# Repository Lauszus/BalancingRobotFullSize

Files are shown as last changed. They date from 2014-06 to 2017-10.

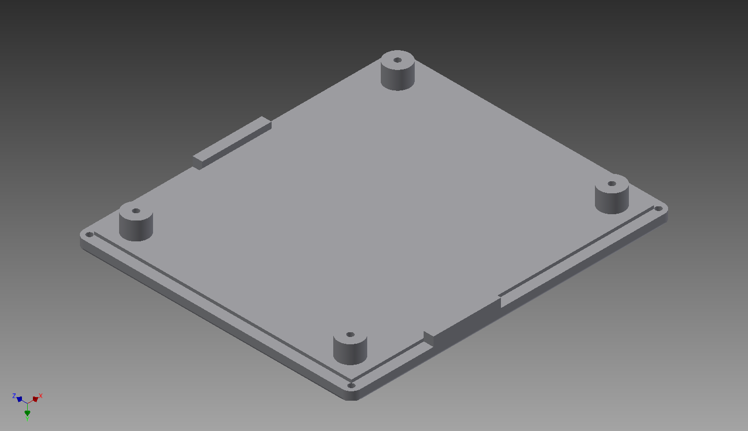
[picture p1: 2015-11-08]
MotorDriverEnclosure/MotorDriverEnclosure_lid.png

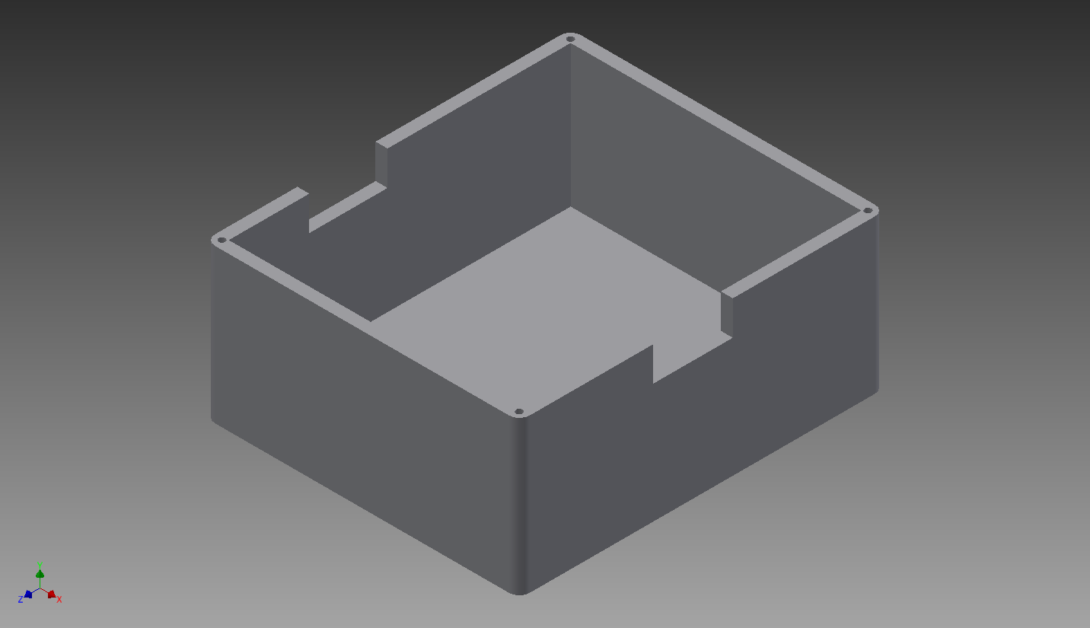
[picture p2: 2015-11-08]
MotorDriverEnclosure/MotorDriverEnclosure.png

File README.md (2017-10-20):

# Balancing robot full size
#### Developed by Kristian Sloth Lauszus and Mads Friis Bornebusch, 2014

The code is released under the GNU General Public License.
_________

This is the code for my full size balancing robot.

Both our paper and poster can be found inside the [Documents](Documents) directory.

Detailed information can be found at the blog post: <http://blog.tkjelectronics.dk/2014/07/full-size-diy-balancing-robot/>.



## Android application



I have also written an Android application for the robot. The source code is available at the following link: <https://github.com/Lauszus/BalancingRobotFullSizeAndroid>.



For more information send me an email at <lauszus@gmail.com>.

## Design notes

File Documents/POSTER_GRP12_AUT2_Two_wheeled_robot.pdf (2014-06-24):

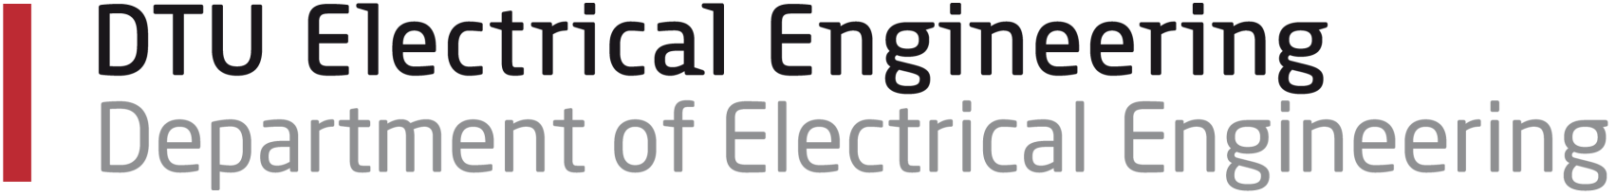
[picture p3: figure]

# Two Wheeled Balancing Robot

# Mads Bornebusch (s123627) Kristian Lauszus (s123808)

Abstract The goal of the project is to build a two wheeled self-balancing robot capable of carrying a person. The dynamics of the robot is found and the system is simulated and stabilized with a controller in Matlab. The robot is programmed in C/C++ on an 8-bit ATmega328P AVR microcontroller. A manually tuned PID-controller is used to keep it balanced. The robot is able to communicate with an

Android device over a two way Bluetooth connection.

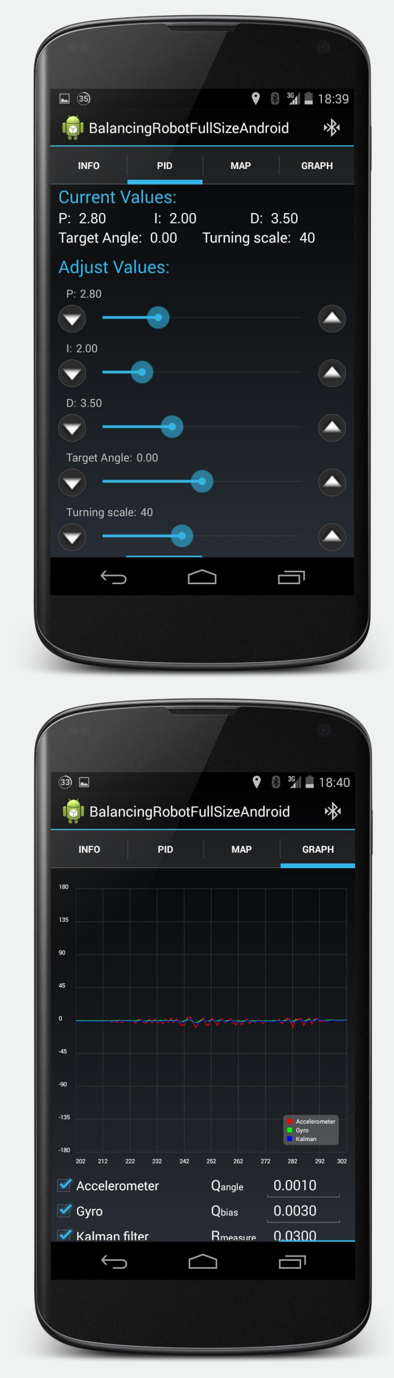
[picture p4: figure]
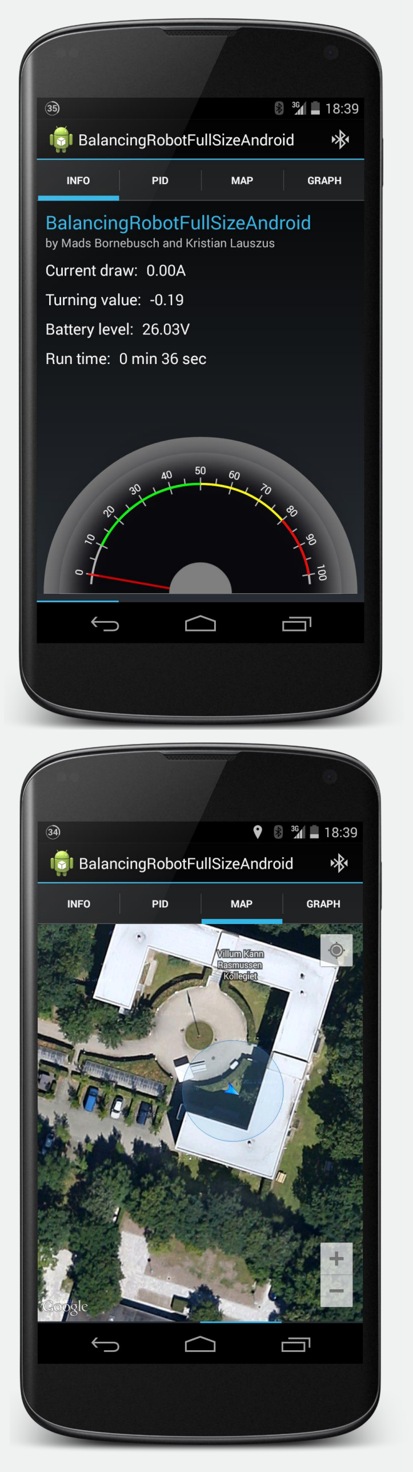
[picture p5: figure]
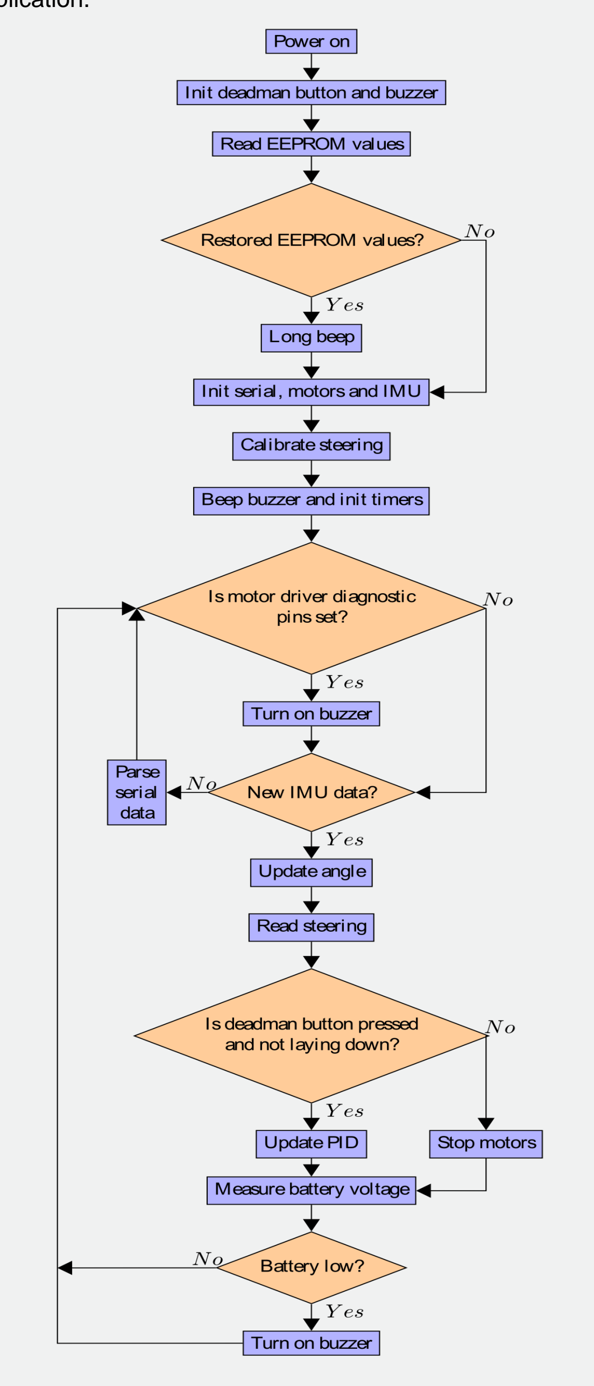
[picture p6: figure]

## Fig. 4 – Andriod Application The figure shows

screenshots of the four different screens in the Android application written for the robot. Top left: This screen shows different values that is sent from the robot to the app. This is general information for the user such as current draw, battery level and PWM-value. Top right: This screen is for adjusting the PID-values for the controller. This is used for tuning the robot to make it balance. The user can also set the target angle and how aggressively the robot is turning. Bottom left: This screen is showing the user a map with the current position of the robot using the Android device’s built in GPS. This can be used for navigation and to see which attractions are nearby. Bottom right: This screen is showing a graph with the angle taken from the gyroscope, the accelerometer and from the Kalman filter.
Protocol: In order to make sure that the data is parsed properly between the robot and the Android application, a protocol for this was implemented. It consists of a constant string header, one byte to indicate the command and one byte indicating the length of the data to follow. After the data there is a checksum calculated by taking XOR of all bytes in the message excluding the header.

## Fig. 3 – Code for the Robot The figure below

shows a flowchart of the code running on the robot. The code for the robot is written in C/C++, using some libraries and functions from the open source platform Arduino. The code consists of a part that initializes the system followed by an infinite loop that balances the robot and sends data to the Android application via Bluetooth. Initialization: When the robot is started up, values are read from the EEPROM, outputs and inputs are initialized on the microcontroller and the steering is calibrated. Main loop: The main loop is checking for IMU-data, updating PID-values, measuring battery voltage and sending serial data via the Bluetooth module to the Android application.

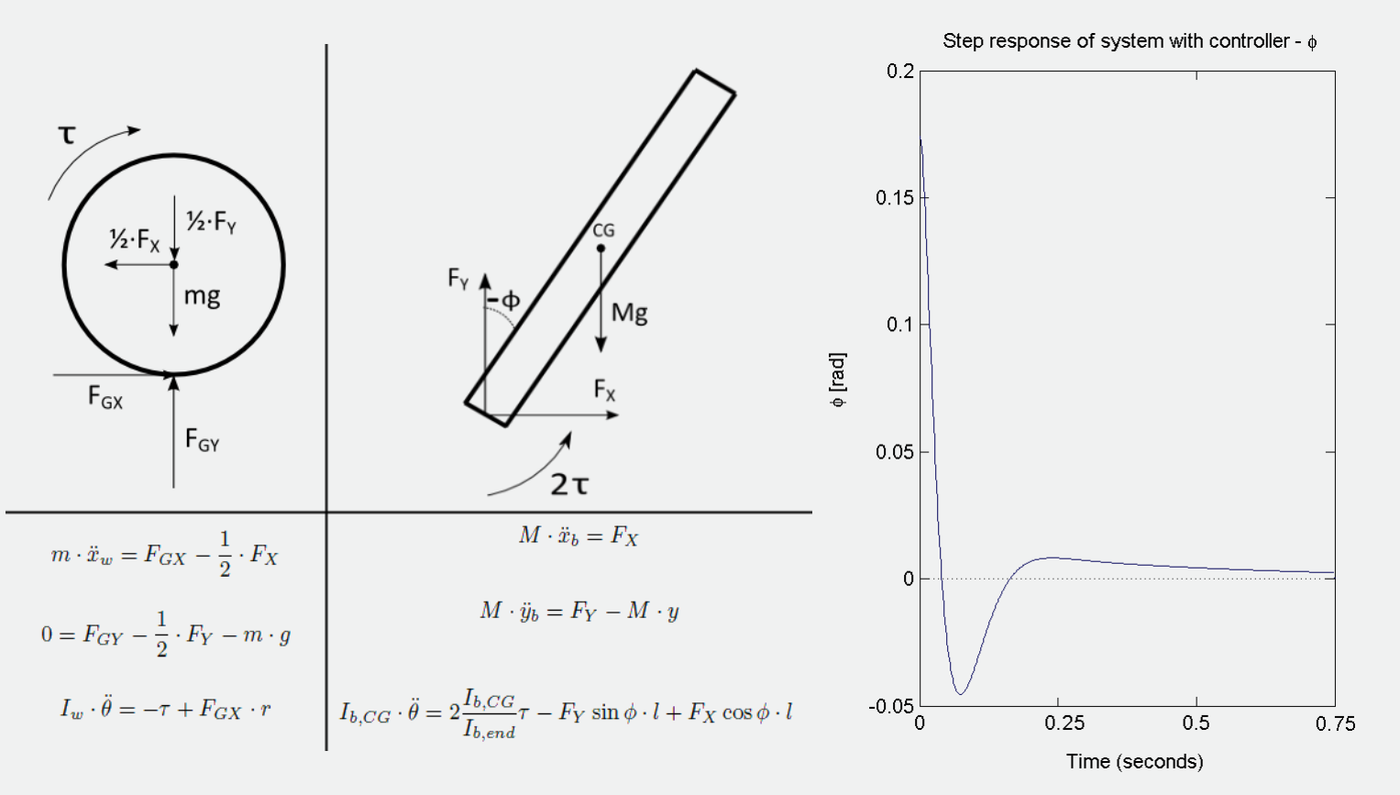
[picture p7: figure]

## Fig. 1 – Model and simulations Using the free

body diagrams to the left, the equations for the robot is set up (left bottom). These lead to a transfer function from τ to φ for the robot and a controller can be designed in Matlab. The controller is designed by choosing ωc which is the cross frequency of the Bode plot of the system. The step response with the controller inserted is shown to the right. It can be seen that it is indeed possible to stabilise the system.

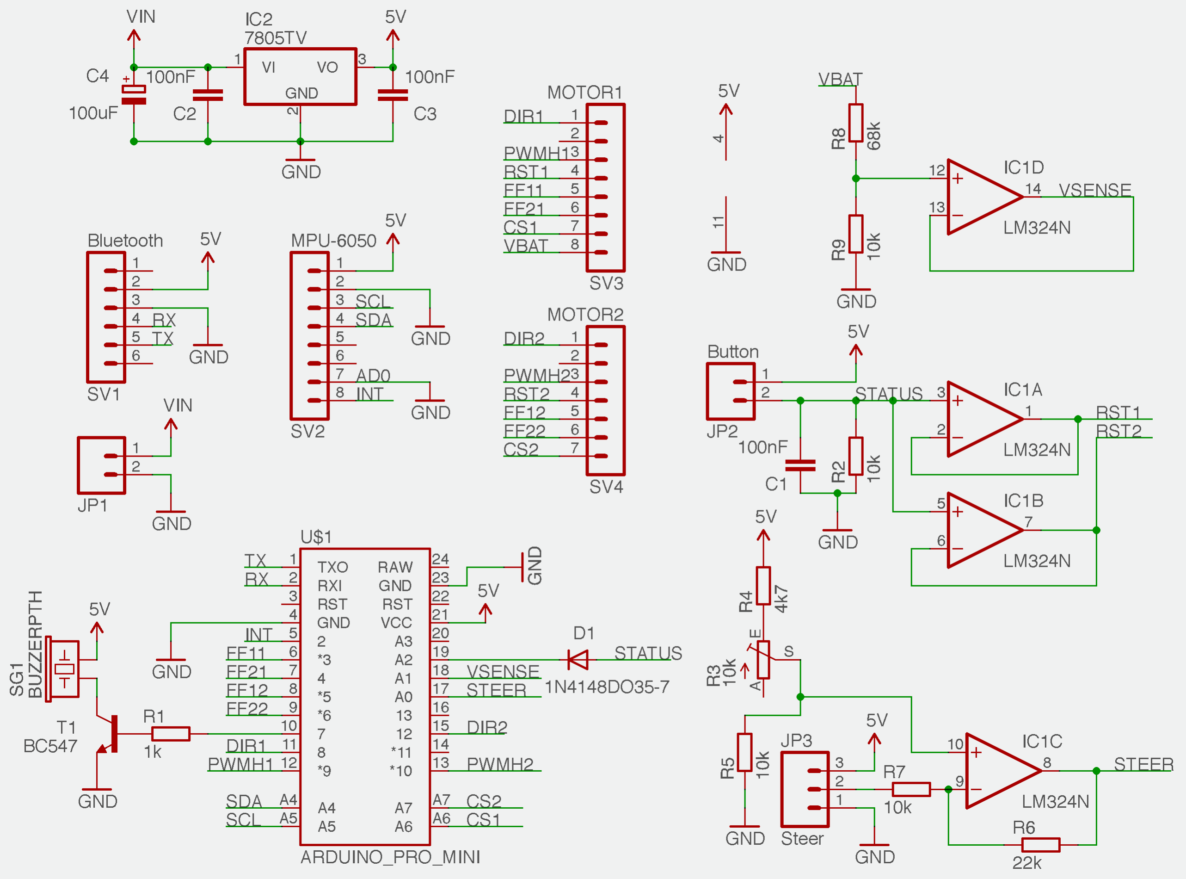
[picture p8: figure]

Fig. 2 – The Hardware The circuit diagram in the figure shows the circuit on the main board of the robot. This contains the microcontroller controlling the robot and is connected to the motor drivers which controls the motors. Important components on the main board:
- Arduino Pro mini
The microcontroller on this board is an 8-bit ATmega328P AVR microcontroller running at 16MHz.
- MPU-6050 Inertial measurement unit (IMU)
The microcontroller is reading from the IMU at 500Hz. The range for the accelerometer is set to ±2g and the range for the gyroscope is set to ±250°/s.
- Bluetooth SPP module
This sends serial data from the microcontroller to the Android application via SPP.
- LM324 Operational Amplifier
The Op-Amp is used as a buffer and an amplifier for the output of the potentiometer used for steering.
- 7805 Linear 5V regulator
This regulator is used to supply power to the components of the main board. It is supplied by the LM2596 (see below). Other important components (not on main board):
- LM2596 Adjustable Switching Regulator
This regulator is used to step down the battery voltage to 8V to supply the 7805. This will minimize the power loss.
- 10 kΩ Potentiometer
The potentiometer measures the angle of the steering rod.
- Momentary push button
This is a deadman button connected to the motor driver resets through a buffer and to the microcontroller.
High power components:
- Motor driver (2): Pololu High-Power Motor Driver 34V/23A Each motor driver is rated to 23A continuous current without a heatsink. We have mounted heatsinks on the motor drivers to increase the continuous current to above 30A.
- Motor (2): MY1020Z 24VDC, 500W
Each of the motors can has a max torque of 12.6 Nm which is 84.4Nm with a 6.7:1 reduction gearing (no mechanical loss). The rated speed is 375rpm. Max current is 26.7A.
- Batteries (3): 3000mAh 6s 20C LiPo pack
Each battery is capable of delivering 60A. This circuit uses three of these batteries in parallel. The voltage of the battery is 21.6V to 25.2V depending on the power left in the battery.

31015 – Introductory project Two Wheeled Balancing Robot Group 12 – AUT2

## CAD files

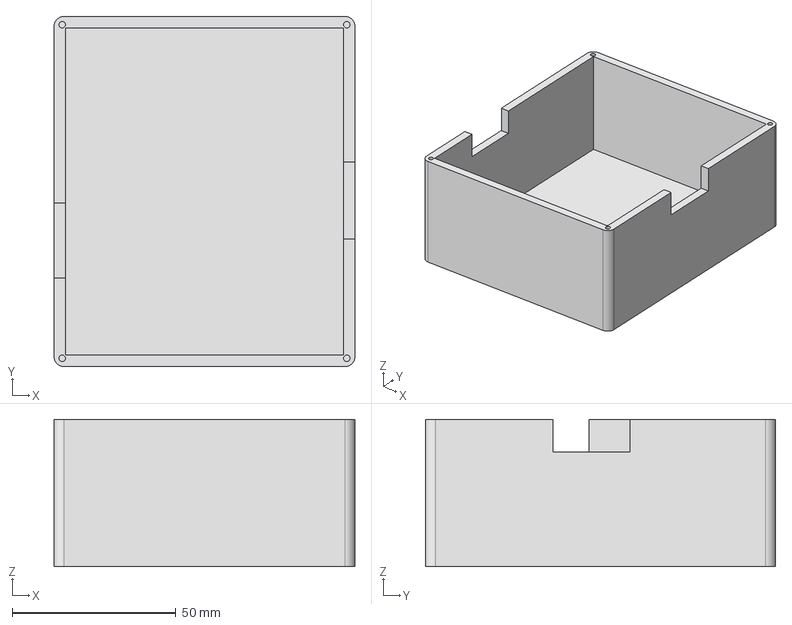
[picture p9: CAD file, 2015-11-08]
MotorDriverEnclosure/MotorDriverEnclosure.stp
92.0 x 107.0 x 45.0 mm

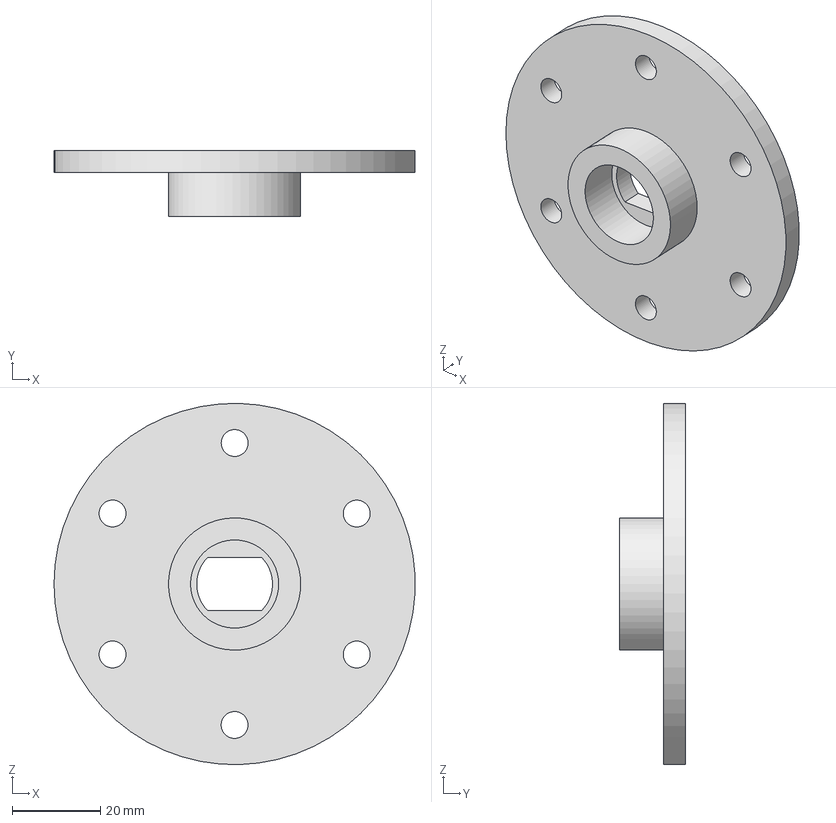
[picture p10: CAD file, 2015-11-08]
MotorHub/MotorHub.stp
81.9 x 15.0 x 82.0 mm

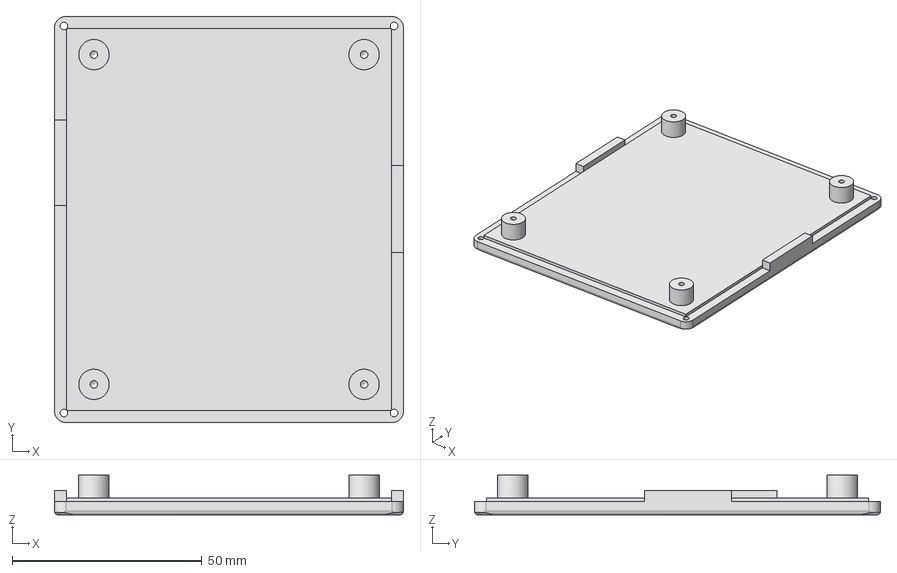
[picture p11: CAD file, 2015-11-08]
MotorDriverEnclosure/MotorDriverEnclosure_lid.stp
92.0 x 107.0 x 10.5 mm

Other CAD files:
MotorDriverEnclosure/MotorDriverEnclosure.ipt
MotorDriverEnclosure/MotorDriverEnclosure.stl
MotorDriverEnclosure/MotorDriverEnclosure_lid.ipt
MotorDriverEnclosure/MotorDriverEnclosure_lid.stl
MotorHub/MotorHub.idw
MotorHub/MotorHub.ipt

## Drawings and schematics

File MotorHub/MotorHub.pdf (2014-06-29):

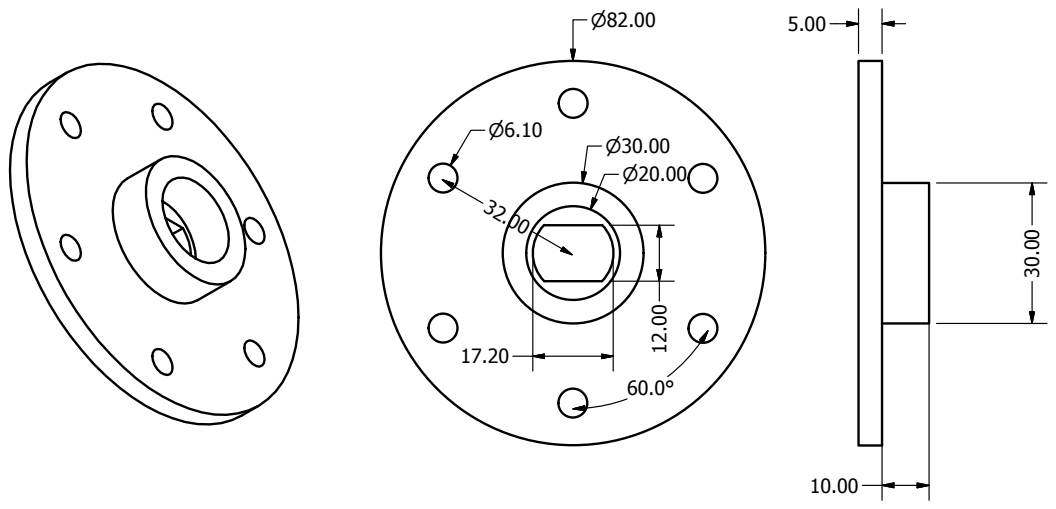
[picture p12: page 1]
SHEET 1 OF 1; DRAWN; CHECKED; MFG; APPROVED; Lauszus; DWG NO MotorHub; TITLE; SIZE C; SCALE; REV

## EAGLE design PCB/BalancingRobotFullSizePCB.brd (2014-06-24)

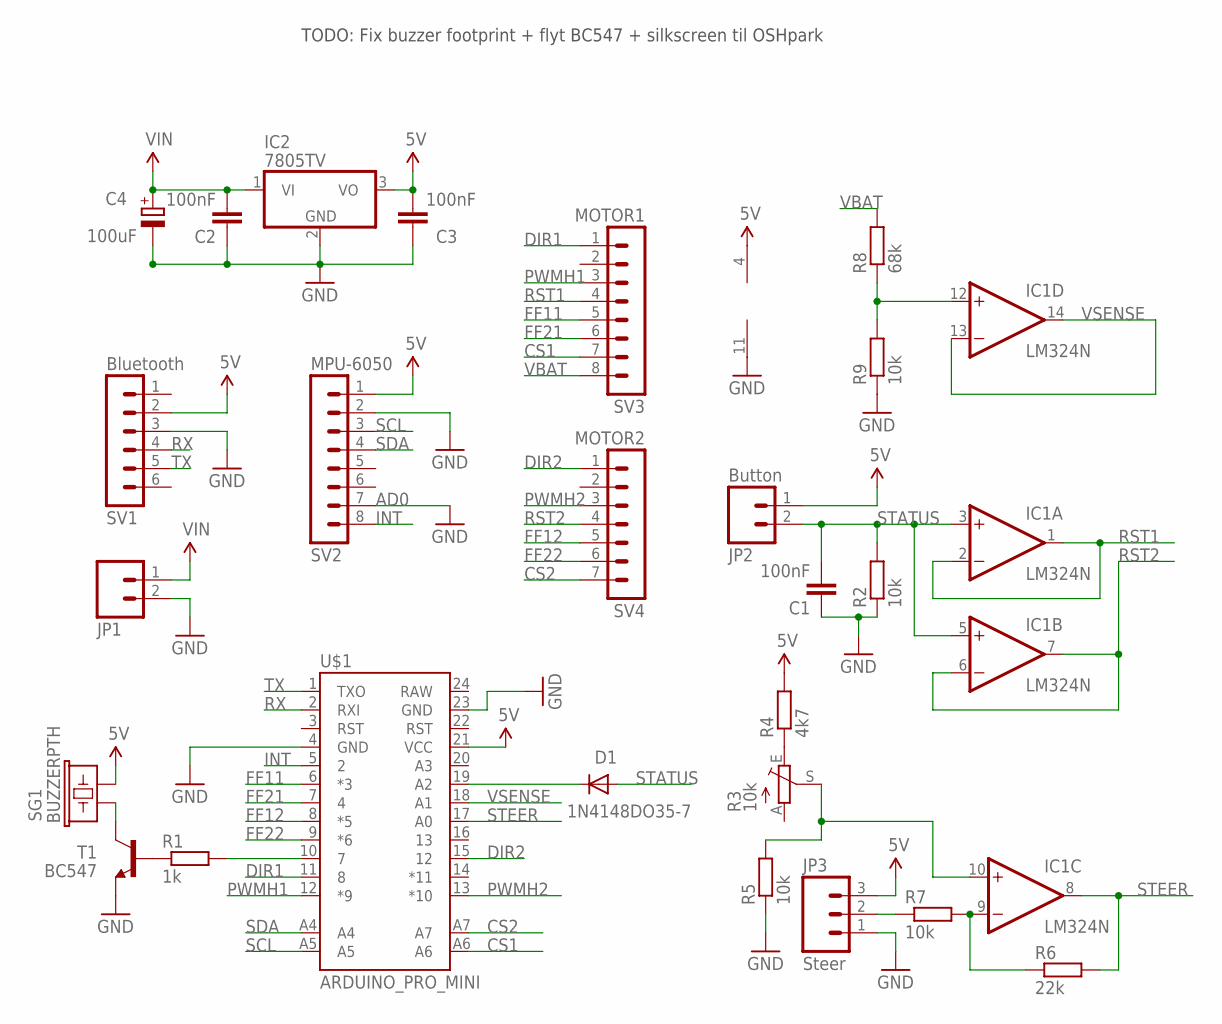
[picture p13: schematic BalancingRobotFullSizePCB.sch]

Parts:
C1, C2, C3: 100nF; C025-025X050
C4: 100uF; E2,5-5
D1: 1N4148DO35-7; DO35-7
IC1: LM324N; DIL14
IC2: 7805TV; TO220V
JP1: M02PTH; 1X02
JP2: Button; 1X02
JP3: Steer; 1X03
R1: 1k; 0207/10
R2, R5, R7, R9: 10k; 0207/10
R3: 10k; B25P
R4: 4k7; 0207/10
R6: 22k; 0207/10
R8: 68k; 0207/10
SG1: BUZZERPTH; BUZZER-12MM
SV1: Bluetooth; MA06-1
SV2: MPU-6050; MA08-1
SV3: MOTOR1; MA08-1
SV4: MOTOR2; MA07-1
T1: BC547; TO92
U$1: ARDUINO_PRO_MINI

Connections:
5V: C3.2, IC1.4 (V+), IC2.3 (VO), JP2.1, JP3.3, R4.2, SG1.- (2), SV1.2, SV2.1, U$1.21 (VCC)
CS1: SV3.7, U$1.A6
CS2: SV4.7, U$1.A7
DIR1: SV3.1, U$1.11 (8)
DIR2: SV4.1, U$1.15 (12)
FF11: SV3.5, U$1.6 (*3)
FF12: SV4.5, U$1.8 (*5)
FF21: SV3.6, U$1.7 (4)
FF22: SV4.6, U$1.9 (*6)
GND: C1.1, C2.1, C3.1, C4.-, IC1.11 (V-), IC2.2 (GND), JP1.2, JP3.1, R2.1, R5.1, R9.1, SV1.3, SV2.2, SV2.7, T1.1 (E), U$1.4 (GND), U$1.23 (GND)
INT: SV2.8, U$1.5 (2)
unnamed: IC1.12 (+IN), R8.1, R9.2
unnamed: D1.C, U$1.19 (A2)
unnamed: R1.1, T1.2 (B)
unnamed: SG1.+ (1), T1.3 (C)
unnamed: R1.2, U$1.10 (7)
unnamed: R3.E, R4.1
unnamed: IC1.10 (+IN), R3.S, R5.2
unnamed: IC1.9 (-IN), R6.1, R7.2
unnamed: JP3.2, R7.1
PWMH1: SV3.3, U$1.12 (*9)
PWMH2: SV4.3, U$1.13 (*10)
RST1: IC1.1 (OUT), IC1.2 (-IN), SV3.4
RST2: IC1.6 (-IN), IC1.7 (OUT), SV4.4
RX: SV1.4, U$1.2 (RXI)
SCL: SV2.3, U$1.A5
SDA: SV2.4, U$1.A4
STATUS: C1.2, D1.A, IC1.3 (+IN), IC1.5 (+IN), JP2.2, R2.2
STEER: IC1.8 (OUT), R6.2, U$1.17 (A0)
TX: SV1.5, U$1.1 (TXO)
VBAT: R8.2, SV3.8
VIN: C2.2, C4.+, IC2.1 (VI), JP1.1
VSENSE: IC1.13 (-IN), IC1.14 (OUT), U$1.18 (A1)

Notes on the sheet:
AD0
TODO: Fix buzzer footprint + flyt BC547 + silkscreen til OSHpark

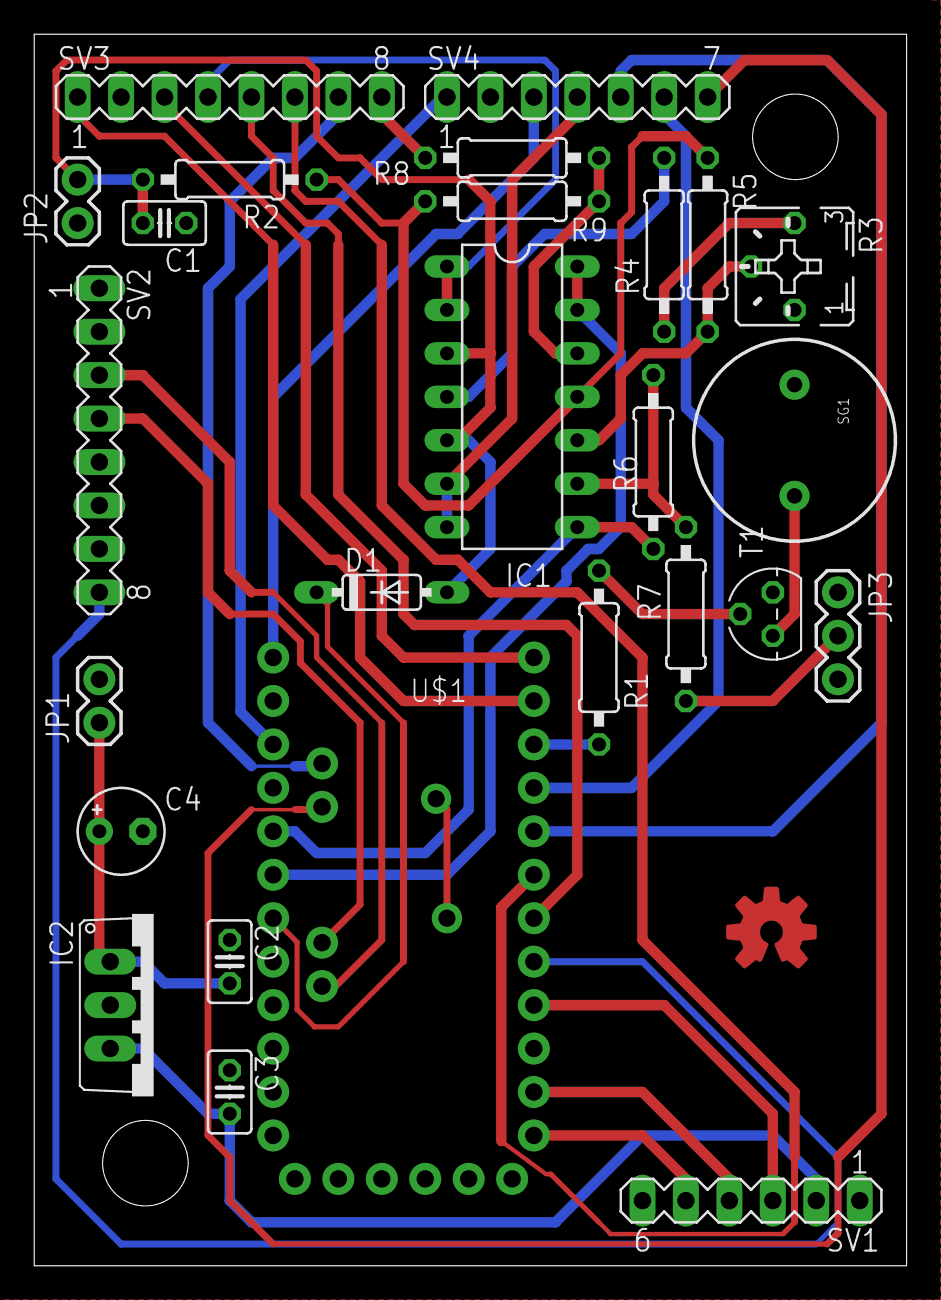
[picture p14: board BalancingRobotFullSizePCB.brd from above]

Board: 2 copper layers, 51.0 x 72.0 mm, 27 parts (0 on the bottom side), 33 nets.

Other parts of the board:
U$4: OSHWLOGO_TOP_0.2

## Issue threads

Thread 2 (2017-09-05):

No need to wait after Wire.requestFrom()

Koepel, 2017-09-05:
In the file "I2C.cpp" there is a timeout with millis() and Wire.available() after the Wire.requestFrom(). That is not needed and can be removed.

When the Wire.requestFrom() returns, the I2C transaction has completely finished and the data is waiting in a buffer in the Wire library.

This is the shortest option:
```
  Wire.requestFrom(address, nbytes, (uint8_t)true); // Send a repeated start and then release the bus after reading
  Wire.readBytes( data, nbytes);
  return 0; // Success
```
This is with using the normal Wire.read() and with testing the number of received bytes:
```
  Wire.requestFrom(address, nbytes, (uint8_t)true); // Send a repeated start and then release the bus after reading
  if (Wire.available() != nbytes) {
    Serial.println(F("i2cRead bus error"));
    return 5; // This error value is not already taken by endTransmission
  }
  for (uint8_t i = 0; i < nbytes; i++) {
    data[i] = Wire.read();
  }
  return 0; // Success
```

Lauszus, 2017-09-06:
@Koepel thanks. I have seen your other issues as well: https://github.com/TKJElectronics/Example-Sketch-for-IMU-including-Kalman-filter/issues/7 and https://github.com/TKJElectronics/KalmanFilter/issues/9, just been to busy to look into it.

Please submit a pull request to: https://github.com/TKJElectronics/KalmanFilter and I'll be happy to merge it.

Lauszus, 2017-09-06:
Btw the reason I didn't use the "readBytes" function was because the code was written before the Wire library inherited the Stream class.

Lauszus, 2017-09-06:
However it should probably return something like this instead:
```
return Wire.readBytes(data, nbytes) != nbytes;
```

Koepel, 2017-09-06:
That is very short and with a test. Nice!

The Wire.readBytes() might not be compatible with every implementation of every Wire compatible library. Personally, I would like to promote the use of Wire.readBytes() if it didn't have consequences: https://github.com/arduino/Arduino/issues/6652

Lauszus, 2017-09-07:
@Koepel can't you just set the timeout to 0 i.e:
```C++
Wire.setTimeout(0);
```
Of course there is going to be a little overhead, but I think we should use it anyway for simplicity.

Koepel, 2017-09-07:
Yes, that would prevent a delay. But I don't know how compatible that is with other (more or less compatible) Wire libraries.

Lauszus, 2018-06-23:
Since this does not have real benefits and the code in the library have been proven to work with multiple different kind of microcontrollers, then I see no real benefit by changing it. If you really want to change it, then you can submit a PR and do some testing.

Closed 2018-06-23.

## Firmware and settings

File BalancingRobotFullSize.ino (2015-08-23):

/* Copyright (C) 2014 Kristian Sloth Lauszus. All rights reserved.

 This software may be distributed and modified under the terms of the GNU
 General Public License version 2 (GPL2) as published by the Free Software
 Foundation and appearing in the file GPL2.TXT included in the packaging of
 this file. Please note that GPL2 Section 2[b] requires that all works based
 on this software must also be made publicly available under the terms of
 the GPL2 ("Copyleft").

 Contact information
 -------------------

 Kristian Sloth Lauszus
 Web      :  http://www.lauszus.com
 e-mail   :  lauszus@gmail.com
*/

#include <Arduino.h>
#include <Wire.h> // Standard Arduino I2C library
#include <Kalman.h>

#include "BalancingRobotFullSize.h"
#include "Pins.h"
#include "Motor.h"
#include "IMU.h"
#include "EEPROM.h"
#include "Protocol.h"
#include "PID.h"

#if defined(__AVR_ATmega328P__) && NUM_ANALOG_INPUTS != 8
#error "Please update the Arduino IDE to version 1.5.7 or above - see: https://github.com/arduino/Arduino/pull/2148"
#endif

double turningValue; // The turning value of the steering rod
uint16_t batteryLevel; // Battery level multiplied by 100 i.e. 24.50V becomes 2450

uint32_t kalmanTimer; // Timer used for the Kalman filter
static uint32_t pidTimer; // Timer used for the PID loop

static bool layingDown; // Used to indicate if the robot is laying down or the button is pressed
static double zeroTurning; // Used for calibration of the steer at startup
static uint8_t batteryCounter;

double getTurning() {
  double turning = (double)analogRead(STEER_PIN) / 204.6 - 2.5; // First convert reading to voltage and then subtract 2.5V, as this is the center of the steering wheel
  turning *= cfg.turningScale; // Scale the turning value, so it will actually turn
  //Serial.println(turning);
  return turning;
}

void setup() {
  /* Setup deadman button */
  deadmanButton::SetDirRead();

  /* Setup buzzer pin */
  buzzer::SetDirWrite();

  /* Read the PID values, target angle and other saved values in the EEPROM */
  if (!checkEEPROMVersion())
    readEEPROMValues(); // Only read the EEPROM values if they have not been restored
  else { // Indicate that the EEPROM values have been reset by turning on the buzzer
    buzzer::Set();
    delay(1000);
    buzzer::Clear();
    delay(100); // Wait a little after the pin is cleared
  }

  initSerial();
  initMotors();
  initIMU();

  zeroTurning = getTurning(); // Calibrate turning

  /* Beep to indicate that it is now ready */
  buzzer::Set();
  delay(100);
  buzzer::Clear();

  /* Setup timing */
  kalmanTimer = micros();
  pidTimer = kalmanTimer;
}

void loop () {
#if 0
  if (leftF1::IsSet() || leftF2::IsSet() || rightF1::IsSet() || rightF2::IsSet()) { // Check the diagnostic pins
    buzzer::Set();
    Serial.print(F("Diagnostic error: "));
    Serial.print(leftF1::IsSet());
    Serial.write('\t');
    Serial.print(leftF2::IsSet());
    Serial.write('\t');
    Serial.print(rightF1::IsSet());
    Serial.write('\t');
    Serial.println(rightF2::IsSet());
  }
#endif

  if (dataReady::IsSet()) { // Check is new data is ready
    updateAngle();

    turningValue = getTurning() - zeroTurning; // Update turning value

    /* Drive motors */
    uint32_t timer = micros();
    // If the robot is laying down, it has to be put in a vertical position before it starts balancing
    // If it's already balancing it has to be ±45 degrees before it stops trying to balance
    // Also make sure that the deadman buttons is pressed
    if (!deadmanButton::IsSet() || (layingDown && (pitch < cfg.targetAngle - 5 || pitch > cfg.targetAngle + 5)) || (!layingDown && (pitch < cfg.targetAngle - 45 || pitch > cfg.targetAngle + 45))) {
      layingDown = true; // The robot is in a unsolvable position, so turn off both motors and wait until it's vertical again
      stopAndReset();
    } else {
      layingDown = false; // It's no longer laying down
      updatePID(cfg.targetAngle, 0 /*targetOffset*/, turningValue, (double)(timer - pidTimer) / 1000000.0);
    }
    pidTimer = timer;

    if (++batteryCounter > 100) {
      batteryCounter = 0;
      batteryLevel = (double)analogRead(VBAT_PIN) / 204.6 * 780.0; // It is connected to a 68k-10k voltage divider and then we multiply this by 100, so 12.50V will be equal to 1250 - the voltage divider is connected to an op amp configured as a buffer
      if (batteryLevel < 2160 && batteryLevel > 500) // Equal to 3.6V per cell (21.60V in total) - don't turn on if it's below 5V, this means that no battery is connected
        buzzer::Set();
      else
        buzzer::Clear();
      // TODO: Calibrate this value
    }
  } else
    parseSerialData(); // Parse incoming serial data
}

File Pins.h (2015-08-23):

/* Copyright (C) 2014 Kristian Sloth Lauszus. All rights reserved.

 This software may be distributed and modified under the terms of the GNU
 General Public License version 2 (GPL2) as published by the Free Software
 Foundation and appearing in the file GPL2.TXT included in the packaging of
 this file. Please note that GPL2 Section 2[b] requires that all works based
 on this software must also be made publicly available under the terms of
 the GPL2 ("Copyleft").

 Contact information
 -------------------

 Kristian Sloth Lauszus
 Web      :  http://www.lauszus.com
 e-mail   :  lauszus@gmail.com
*/

#ifndef _pins_h_
#define _pins_h_

// I use the pins defined in avrpins.h from the USB Host library which I am also one of the developers of
// This allows to read and write directly to the port registers instead of using Arduino's slow digitalRead()/digitalWrite() functions
// The original source is available here: https://github.com/felis/USB_Host_Shield_2.0/blob/master/avrpins.h
// I do this to save processing power - see this page for more information: http://www.billporter.info/ready-set-oscillate-the-fastest-way-to-change-arduino-pins/
// Also see the Arduino port manipulation guide: http://www.arduino.cc/en/Reference/PortManipulation
#include "avrpins.h"

/* Pin connect to INT on the MPU-6050 */
#define dataReady P2

#define buzzer P7 // Buzzer used for audio feedback
#define deadmanButton P16 // (A2) Deadman button

/* Left motor */
#define leftDir P12
#define leftPWM P10
#define leftPWMReg OCR1B

/* Right motor */
#define rightDir P8
#define rightPWM P9
#define rightPWMReg OCR1A

/* Pins connected to the motor drivers diagnostic pins */
#define leftF1 P5
#define leftF2 P6

#define rightF1 P3
#define rightF2 P4

/* Analog pins */
#define STEER_PIN A0
#define VBAT_PIN  A1
#define CS1_PIN   A6
#define CS2_PIN   A7

#endif

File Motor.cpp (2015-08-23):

/* Copyright (C) 2014 Kristian Sloth Lauszus. All rights reserved.

 This software may be distributed and modified under the terms of the GNU
 General Public License version 2 (GPL2) as published by the Free Software
 Foundation and appearing in the file GPL2.TXT included in the packaging of
 this file. Please note that GPL2 Section 2[b] requires that all works based
 on this software must also be made publicly available under the terms of
 the GPL2 ("Copyleft").

 Contact information
 -------------------

 Kristian Sloth Lauszus
 Web      :  http://www.lauszus.com
 e-mail   :  lauszus@gmail.com
*/

#include "Motor.h"
#include "Pins.h"

static const uint16_t PWM_FREQUENCY = 20000; // Set the PWM frequency to 20kHz
static const uint16_t PWMVALUE = F_CPU / PWM_FREQUENCY / 2; // The frequency is given by F_CPU/(2*N*ICR) - where N is the prescaler, prescaling is used so the frequency is given by F_CPU/(2*ICR) - ICR = F_CPU/PWM_FREQUENCY/2

void setPWM(Command motor, uint16_t dutyCycle);

void initMotors() {
  /* Set the motor driver diagnostic pins to inputs */
  leftF1::SetDirRead();
  leftF2::SetDirRead();
  rightF1::SetDirRead();
  rightF2::SetDirRead();

  /* Setup motor pins to output */
  leftPWM::SetDirWrite();
  leftDir::SetDirWrite();
  rightPWM::SetDirWrite();
  rightDir::SetDirWrite();

  /* Set PWM frequency to 20kHz - see the datasheet http://www.atmel.com/Images/Atmel-8271-8-bit-AVR-Microcontroller-ATmega48A-48PA-88A-88PA-168A-168PA-328-328P_datasheet_Complete.pdf page 128-138 */
  // Set up PWM, Phase and Frequency Correct on pin 9 (OC1A) & pin 10 (OC1B) with ICR1 as TOP using Timer1
  TCCR1B = (1 << WGM13) | (1 << CS10); // Set PWM Phase and Frequency Correct with ICR1 as TOP and no prescaling
  ICR1 = PWMVALUE; // ICR1 is the TOP value - this is set so the frequency is equal to 20kHz

  /* Enable PWM on pin 9 (OC1A) & pin 10 (OC1B) */
  // Clear OC1A/OC1B on compare match when up-counting
  // Set OC1A/OC1B on compare match when down-counting
  TCCR1A = (1 << COM1A1) | (1 << COM1B1);

  stopMotor(left);
  stopMotor(right);
}

void moveMotor(Command motor, Command direction, double speedRaw) { // Speed is a value in percentage 0-100%
  if (speedRaw > 100)
    speedRaw = 100.0;
  setPWM(motor, speedRaw * ((double)PWMVALUE) / 100.0); // Scale from 0-100 to 0-PWMVALUE
  if (motor == left) {
    if (direction == forward)
      leftDir::Clear();
    else
      leftDir::Set();
  } else {
    if (direction == forward)
      rightDir::Set();
    else
      rightDir::Clear();
  }
}

void stopMotor(Command motor) {
  setPWM(motor, 0); // Set low
}

void setPWM(Command motor, uint16_t dutyCycle) { // dutyCycle is a value between 0-ICR1
  if (motor == left)
    leftPWMReg = dutyCycle;
  else
    rightPWMReg = dutyCycle;
}

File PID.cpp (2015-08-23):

/* Copyright (C) 2014 Kristian Sloth Lauszus. All rights reserved.

 This software may be distributed and modified under the terms of the GNU
 General Public License version 2 (GPL2) as published by the Free Software
 Foundation and appearing in the file GPL2.TXT included in the packaging of
 this file. Please note that GPL2 Section 2[b] requires that all works based
 on this software must also be made publicly available under the terms of
 the GPL2 ("Copyleft").

 Contact information
 -------------------

 Kristian Sloth Lauszus
 Web      :  http://www.lauszus.com
 e-mail   :  lauszus@gmail.com
*/

#include <Arduino.h>

#include "PID.h"
#include "IMU.h"
#include "Motor.h"
#include "EEPROM.h"

double PIDValue; // Calculated PID value

static double lastError; // Store last angle error
static double integratedError; // Store integrated error

static double currentSpeed; // Estimated speed from PWM value

void updatePID(double restAngle, double offset, double turning, double dt) {
  /* Update PID values */
  double error = (restAngle - pitch);
  double pTerm = cfg.Kp * error;
  integratedError += error * dt;
  //integratedError = constrain(integratedError, -1.0, 1.0); // Limit the integrated error
  double iTerm = (cfg.Ki * 100.0) * integratedError;
  double dTerm = (cfg.Kd / 100.0) * (error - lastError) / dt;
  lastError = error;
  PIDValue = pTerm + iTerm + dTerm;

  currentSpeed = (currentSpeed + PIDValue * 0.004) * 0.999; // TODO: Explain this
  //currentSpeed = constrain(currentSpeed, -50, 50);

  //Serial.print(PIDValue); Serial.write('\t'); Serial.print(currentSpeed); Serial.write('\t');

  PIDValue += currentSpeed;

  //Serial.println(PIDValue);

#if 0 // TODO: Estimate velocity and steer
  /* Steer robot sideways */
  if (turning < 0) { // Left
    turning += abs((double)wheelVelocity / velocityScaleTurning); // Scale down at high speed
    if (turning > 0)
      turning = 0;
  } else if (turning > 0) { // Right
    turning -= abs((double)wheelVelocity / velocityScaleTurning); // Scale down at high speed
    if (turning < 0)
      turning = 0;
  }
#endif

  // TODO: Turn opposite when going backwards
  double PIDLeft = PIDValue - turning;
  double PIDRight = PIDValue + turning;

  PIDLeft *= cfg.leftMotorScaler; // Compensate for difference in some of the motors
  PIDRight *= cfg.rightMotorScaler;

  //Serial.print(PIDLeft); Serial.write('\t'); Serial.println(PIDRight);

  /* Set PWM Values */
  if (PIDLeft >= 0)
    moveMotor(left, forward, PIDLeft);
  else
    moveMotor(left, backward, -PIDLeft);
  if (PIDRight >= 0)
    moveMotor(right, forward, PIDRight);
  else
    moveMotor(right, backward, -PIDRight);
}

void stopAndReset() {
  PIDValue = 0;
  stopMotor(left);
  stopMotor(right);
  lastError = 0;
  integratedError = 0;
  currentSpeed = 0;
}

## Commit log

2014-05-30 Read deadmanButton. This is used to reset all values.
    [BalancingRobotFullSize.ino]
2014-05-30 Add short delay until INT is used on the MPU-6050
    [BalancingRobotFullSize.ino]
2014-05-31 Set I2C to send stop by default
2014-05-31 Move all pin defined into it's own header
2014-05-31 Decreased I2C_TIMEOUT
    It should never take this long
2014-05-31 Moved stopAndReset function into PID.cpp
2014-06-05 Increased I2C_TIMEOUT again
    Also converted from uint16_t to uint8_t
2014-06-05 Swap left and right motor
    [Motor.cpp, PID.cpp, Pins.h]
2014-06-05 Calibrate turning at startup
2014-06-09 Updated some comments and improved slightly sendData on some devices
2014-06-15 Updated some comments and replaced for loop with for each loops in Processing code
    [ProcessingApp.pde, Protocol.cpp, Protocol.pde]
2014-06-16 Can now send speed, current draw, turning value, battery level and run time via serial
    Still need to implement current and battery level measurement on a hardware level
2014-06-16 Can now send IMU data
2014-06-17 Measure current draw and battery voltage
2014-06-17 Pin relocation
2014-06-17 Multiply battery level by 100, as the rest of the data
    Also forgot to multiply turningValue by 100
2014-06-18 Define all analog pins in Pins.h
    Also used 68k resistor instead of 47k in voltage divider
2014-06-18 Start the buzzer if the voltage get's to low
    Also check if deadman buttons is pressed before taking current sense measurement
    [BalancingRobotFullSize.ino, Pins.h, Protocol.cpp]
2014-06-18 Only parse incoming serial data if it doesn't update the IMU values
    [BalancingRobotFullSize.ino]
2014-06-18 Make sure that it will never send out info and imu values in the same loop
2014-06-18 Make sure the voltage is also above 5V before starting the buzzer
    [BalancingRobotFullSize.ino]
2014-06-24 Don't divide the current draw
2014-06-24 Deadman button pin location was changed
    Also fixed some comments
    [IMU.cpp, Pins.h]
2014-06-24 Added PCB
    [BalancingRobotFullSizePCB.brd, BalancingRobotFullSizePCB.sch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]
2014-06-25 The IMU was mounted upside down on the final PCB
    Also turning was inverted after we soldered everything together
    [IMU.cpp, PID.cpp]
2014-06-25 Move currentSpeed calculation up before turning
2014-06-29 Uploaded 3D drawing of motor hub
    [MotorHub.idw, MotorHub.ipt, MotorHub.stp]
2014-07-02 Added image of schematic
2014-07-07 Check if NUM_ANALOG_INPUTS is equal to 8
    If not they would need to update the Arduino IDE - see: https://github.com/arduino/Arduino/pull/2148
2014-07-07 Use Wire.setClock to set I2C frequency when using Arduino 1.5.7 or above
    See: https://github.com/arduino/Arduino/pull/1912
2014-07-07 Updated some comments and added static to PWM_FREQUENCY and PWMVALUE
2014-07-07 Move calculation of accAngle inside updateIMUValues() and check if data is ready when calibrating gyro
2014-07-07 The motors are turning opposite, so the other current sense value must be subtracted
2015-11-08 Renamed directory with 3D model for the motor hub
    [MotorHub.idw, MotorHub.ipt, MotorHub.stp]
2015-11-08 Uploaded 3D model of motor driver enclosure
    [MotorDriverEnclosure.ipt, MotorDriverEnclosure.stl, MotorDriverEnclosure.stp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]

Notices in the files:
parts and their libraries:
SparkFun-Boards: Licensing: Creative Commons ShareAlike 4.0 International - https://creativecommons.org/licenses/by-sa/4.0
